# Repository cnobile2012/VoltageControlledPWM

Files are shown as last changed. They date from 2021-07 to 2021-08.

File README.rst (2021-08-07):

***************************************
Voltage-Controlled PWM Motor Controller
***************************************
The MIT License (MIT)

This circuit can supply either a 3.3 or 5 volt logic level PWM signal
depending on the reference voltage used. The voltage control input can also
be driven with either a 3.3 or 5 volt logic level signal depending on the
how the circuit is calibrated.

The PWM frequency can be adjusted in the range of 25K Hertz.

=======
LTspice
=======

Spice files for testing the circuit viability.

=====
KiCAD
=====

KiCAD files of the schematic and PCB.

========================
Calibration Instructions
========================

Test Equipment
--------------

  1. +12 and -12 Volt bench power supply.
  2. +5 or +3.3 Volt bench power supply.
  3. Variable voltage bench supply (0V-3.3V or 0V-5V).
  4. Multimeter
  5. Oscilloscope
  6. Frequency Counter (Optional--Can use the scope)

First, be sure your dual voltage power supply is as close to +12 and -12 volts
as possible. This will also be true in the actual environment that this PWM
will call home. If there is a slight offset between the absolute + and -
voltages there will also be a slight offset between the internal zero crossing
point of the triangle wave. Resistor R6 (460) can be adjusted to compensate for
this. The two trimmers R9 and R11 can also affect a slightly off zero crossing
by adjusting the complete on or off of the PWM, that is where a 0 control
voltage causes the output PWM to be 0 volts and the max 3.3/5 control voltage
causes the PWM to be 3.3/5 volts.

Calibration
-----------

  1. The R3 trimmer is used to adjust the internal triangle reference voltage.
     This should nominally be 10 volts peak-to-peak with the trimmer set to
     approximately 250K. Put your scope probes between TP2 (Triangle Wave) and
     TP0 (GND) then adjust R3.
  2. The R1 trimmer is used to adjust the frequency of the triangle wave. This
     should nominally be 25K Hertz with the trimmer set to approximately 24K.
     Put your scope or frequency counter probes between TP2 (Triangle Wave)
     and TP0 (GND) then adjust R1.
  3. The R9 trimmer is used to adjust the symmetry of the sweep voltage. This
     is the Control Voltage that adjusts the modulation of the PWM frequency.
     Adjust the variable power supply to 50% of 3.3V (1.65V) or 5V (2.5V)
     depending on your drive voltage then attach the supply to J3 and attach
     the multimeter probes to TP3 (Sweep) and TP0 (GND). Double check that the
     supply voltage is at 50% of your driving voltage then adjust R9 so the
     voltage on the multimeter is as close to 0 (zero) volts as possible.
  4. The R11 trimmer is used to set the peak-to-peak of the sweep voltage. Set
     the variable power supply to your drive voltage 5V or 3.3V and attach it
     to J3 (Voltage Control Input). Attach the multimeter probes to TP3 (Sweep)
     and TP0 (GND). Adjust R11 so that the multimeter shows plus 5V. Adjust the
     supply to 0 (zero) volts (or short the two pins on J3) and check that the
     voltage on the multimeter is -5V. See note 1 below.
  5. Check the PWM. Adjust the supply voltage to 50% as was done in step 3
     above and check that the PWM is 50%, then adjust the supply to 0 (zero)
     (or just short the two pins on J3) Check that the PWM is 0 (zero) volts.

Notes:

  1. In order to get 0 (full off) and 5/3.3 Volts (full on), on the PWM the
     sweep voltage may need to be slightly more than 10V peak-to-peak (R11)
     assuming the maximum triangle wave voltage is still 10V
     peak-to-peak. Adjusting the zero crossing with R9 may also be necessary.
  2. TP1 provides a square wave output, however it is not used in any of the
     calibrations.
  3. On Version 1.0 of the PCB the silk screen for the TPs (test points) are
     rather small and difficult to read. This will be fixed in version 2.0 of
     the PCB. The photos below should help with identifying which TP is which.

==============
PCBs Version 1
==============

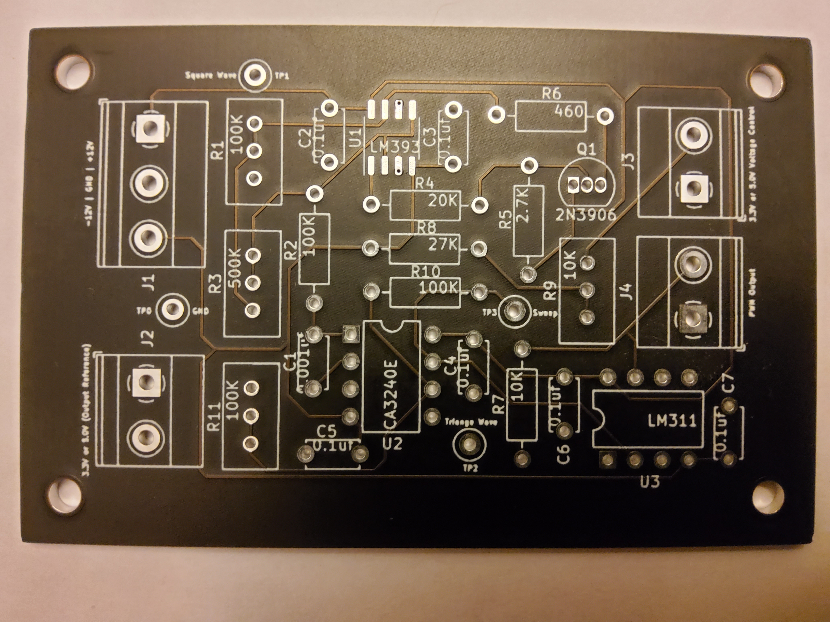
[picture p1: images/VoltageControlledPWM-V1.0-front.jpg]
Circuit board frontside image


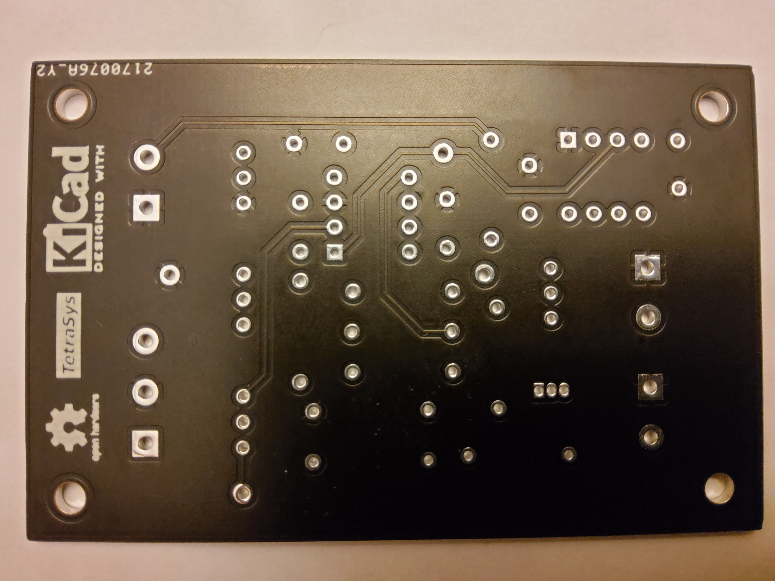
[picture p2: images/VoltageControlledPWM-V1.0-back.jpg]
Circuit board backside image


=========
Schematic
=========

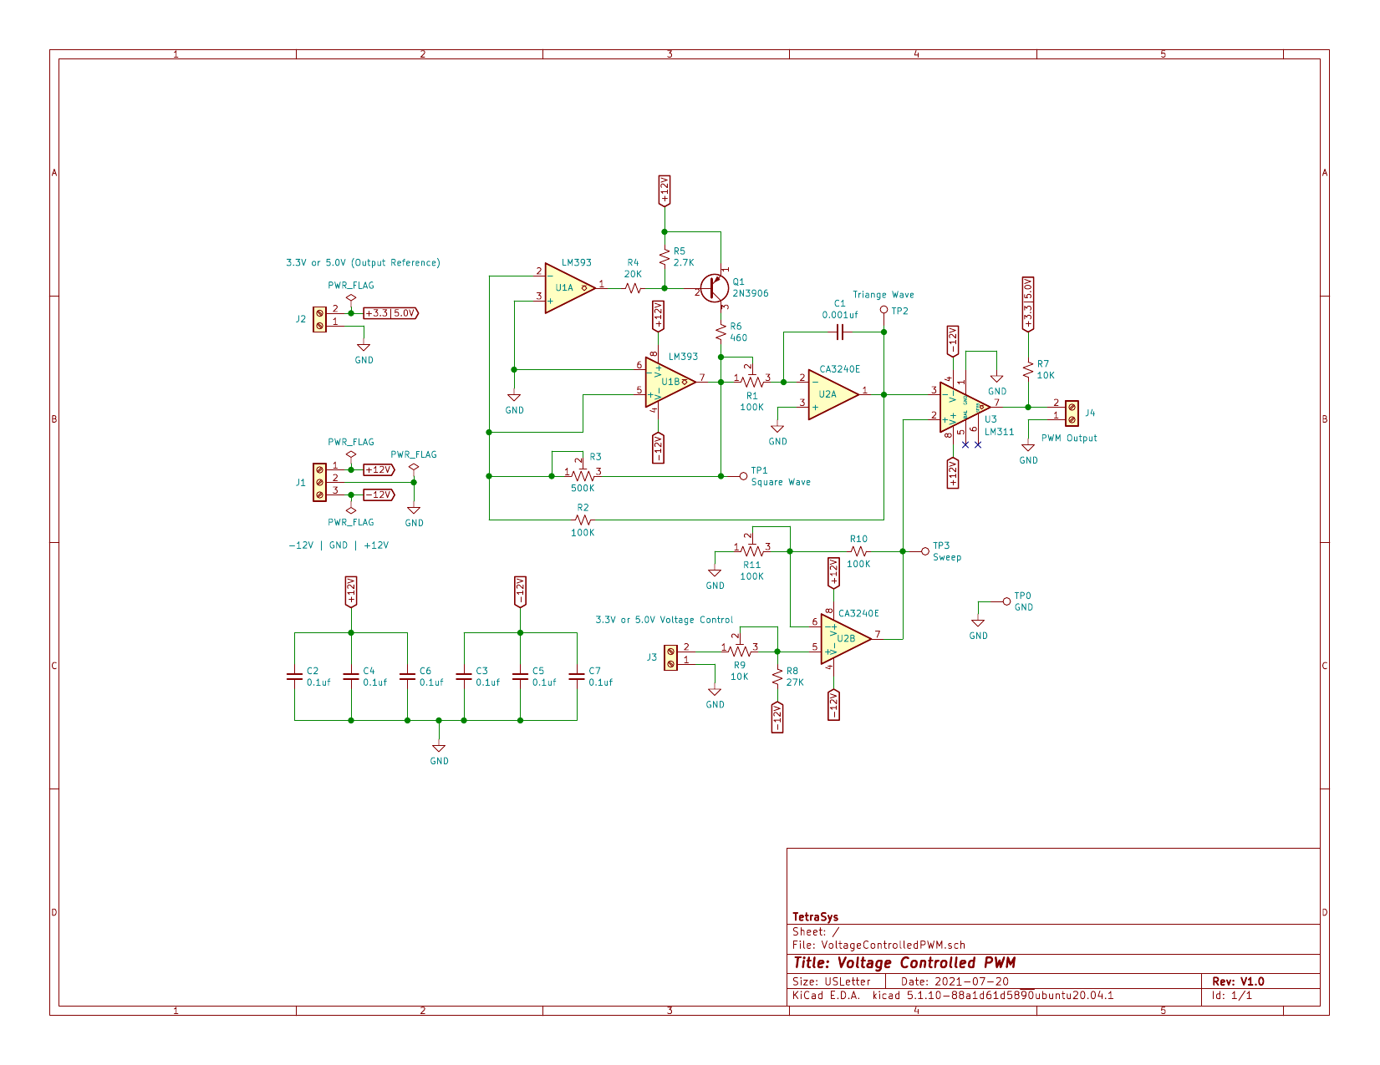
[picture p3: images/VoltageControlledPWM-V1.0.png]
Schematic


I want to give attribution to `Zero999 <https://www.eevblog.com/forum/beginners/simple-analog-function-generator-design/msg1174983/#msg1174983>`_
for the oscillator part of my circuit.

Feel free to contact me at: carl dot nobile at gmail.com

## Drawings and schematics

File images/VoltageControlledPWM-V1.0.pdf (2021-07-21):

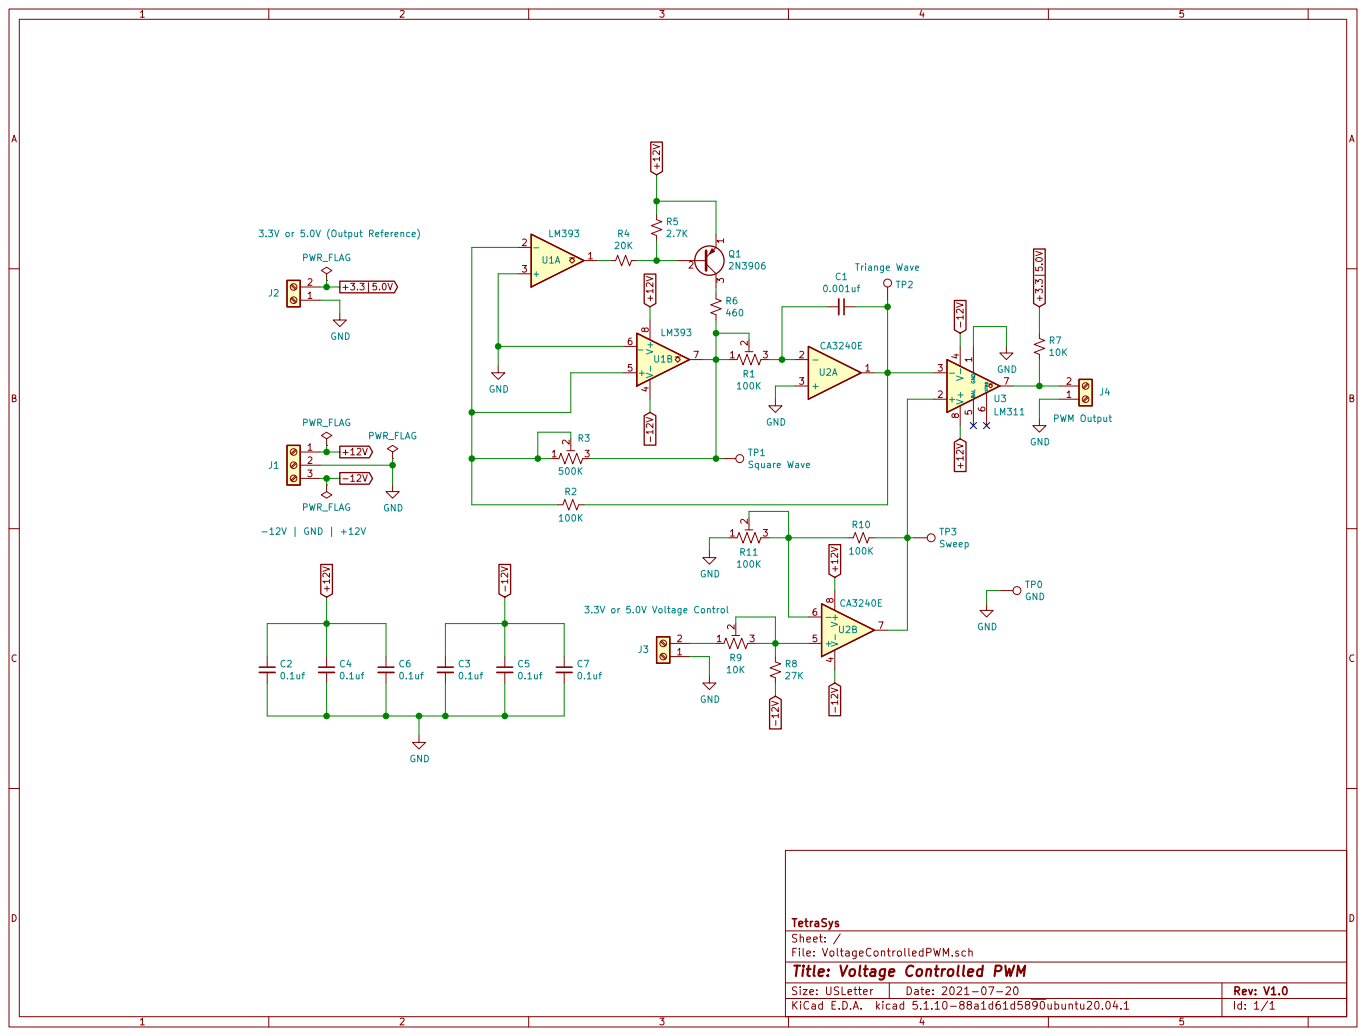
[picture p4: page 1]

TP3 Sweep TP2 Triange Wave TP1 Square Wave

File: VoltageControlledPWM.sch Sheet: / TetraSys

Id: 1/1 Title: Voltage Controlled PWM

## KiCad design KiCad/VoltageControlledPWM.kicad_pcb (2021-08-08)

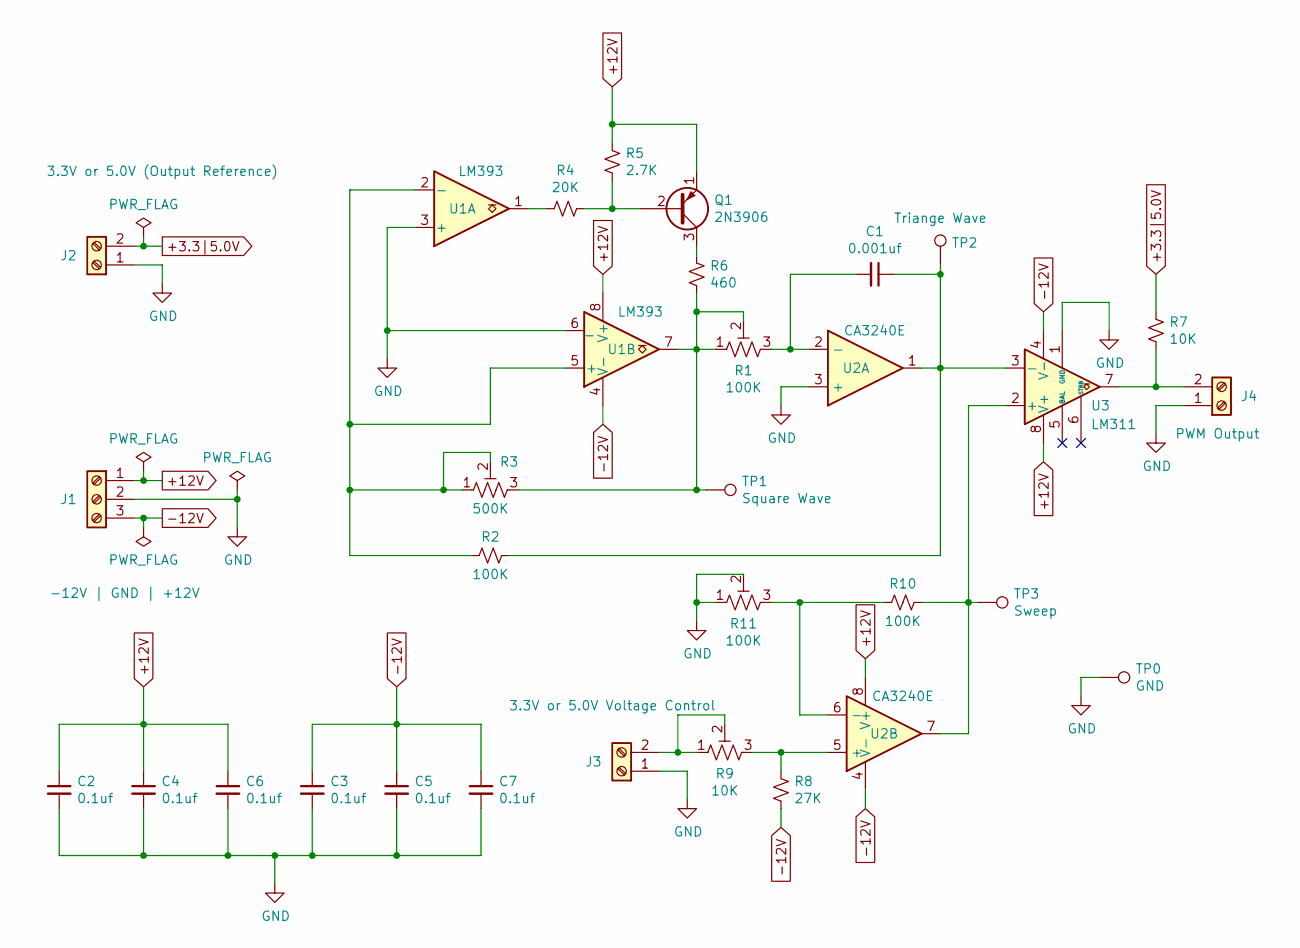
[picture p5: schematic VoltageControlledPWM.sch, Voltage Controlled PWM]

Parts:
C1: 0.001uf; C_Disc_D4.7mm_W2.5mm_P5.00mm
C2, C3, C4, C5, C6, C7: 0.1uf; C_Disc_D4.7mm_W2.5mm_P5.00mm
J1: -12V | GND | +12V; TerminalBlock_Phoenix_MKDS-1,5-3-5.08_1x03_P5.08mm_Horizont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
J2: 3.3V or 5.0V (Output Reference); TerminalBlock_Phoenix_MKDS-1,5-2-5.08_1x02_P5.08mm_Horizont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
J3: 3.3V or 5.0V Voltage Control; TerminalBlock_Phoenix_MKDS-1,5-2-5.08_1x02_P5.08mm_Horizont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
J4: PWM Output; TerminalBlock_Phoenix_MKDS-1,5-2-5.08_1x02_P5.08mm_Horizont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
Q1: 2N3906; TO-92_Inline
R1, R11: 100K; Potentiometer_Bourns_3296W_Vertical
R2, R10: 100K; R_Axial_DIN0207_L6.3mm_D2.5mm_P10.16mm_Horizontal
R3: 500K; Potentiometer_Bourns_3296W_Vertical
R4: 20K; R_Axial_DIN0207_L6.3mm_D2.5mm_P10.16mm_Horizontal
R5: 2.7K; R_Axial_DIN0207_L6.3mm_D2.5mm_P10.16mm_Horizontal
R6: 460; R_Axial_DIN0207_L6.3mm_D2.5mm_P10.16mm_Horizontal
R7: 10K; R_Axial_DIN0207_L6.3mm_D2.5mm_P10.16mm_Horizontal
R8: 27K; R_Axial_DIN0207_L6.3mm_D2.5mm_P10.16mm_Horizontal
R9: 10K; Potentiometer_Bourns_3296W_Vertical
TP0: GND; TestPoint_Loop_D2.50mm_Drill1.0mm
TP1: Square Wave; TestPoint_Loop_D2.50mm_Drill1.0mm
TP2: Triange Wave; TestPoint_Loop_D2.50mm_Drill1.0mm
TP3: Sweep; TestPoint_Loop_D2.50mm_Drill1.0mm
U1: LM393; SO-8_3.9x4.9mm_P1.27mm
U2: CA3240E; DIP-8_W7.62mm
U3: LM311; DIP-8_W7.62mm

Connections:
+3.3|5.0V: J2.2, R7.1
+12V: C2.1, C4.1, C6.1, J1.1, Q1.1 (E), R5.1, U1.8 (V+), U2.8 (V+), U3.8 (V+)
-12V: C3.1, C5.1, C7.1, J1.3, R8.2, U1.4 (V-), U2.4 (V-), U3.4 (V-)
GND: C2.2, C3.2, C4.2, C5.2, C6.2, C7.2, J1.2, J2.1, J3.1, J4.1, R11.1, R11.2, TP0.1, U1.3 (+), U1.6 (_), U2.3 (+), U3.1 (GND)
unnamed: C1.1, R2.1, TP2.1, U2.1, U3.3 (-)
unnamed: C1.2, R1.3, U2.2 (-)
unnamed: J3.2, R9.1, R9.2
unnamed: J4.2, R7.2, U3.7
unnamed: Q1.2 (B), R4.1, R5.2
unnamed: Q1.3 (C), R6.1
unnamed: R1.1, R1.2, R3.3, R6.2, TP1.1, U1.7
unnamed: R2.2, R3.1, R3.2, U1.2 (-), U1.5 (+)
unnamed: R4.2, U1.1
unnamed: R8.1, R9.3, U2.5 (+)
unnamed: R10.1, TP3.1, U2.7, U3.2 (+)
unnamed: R10.2, R11.3, U2.6 (-)

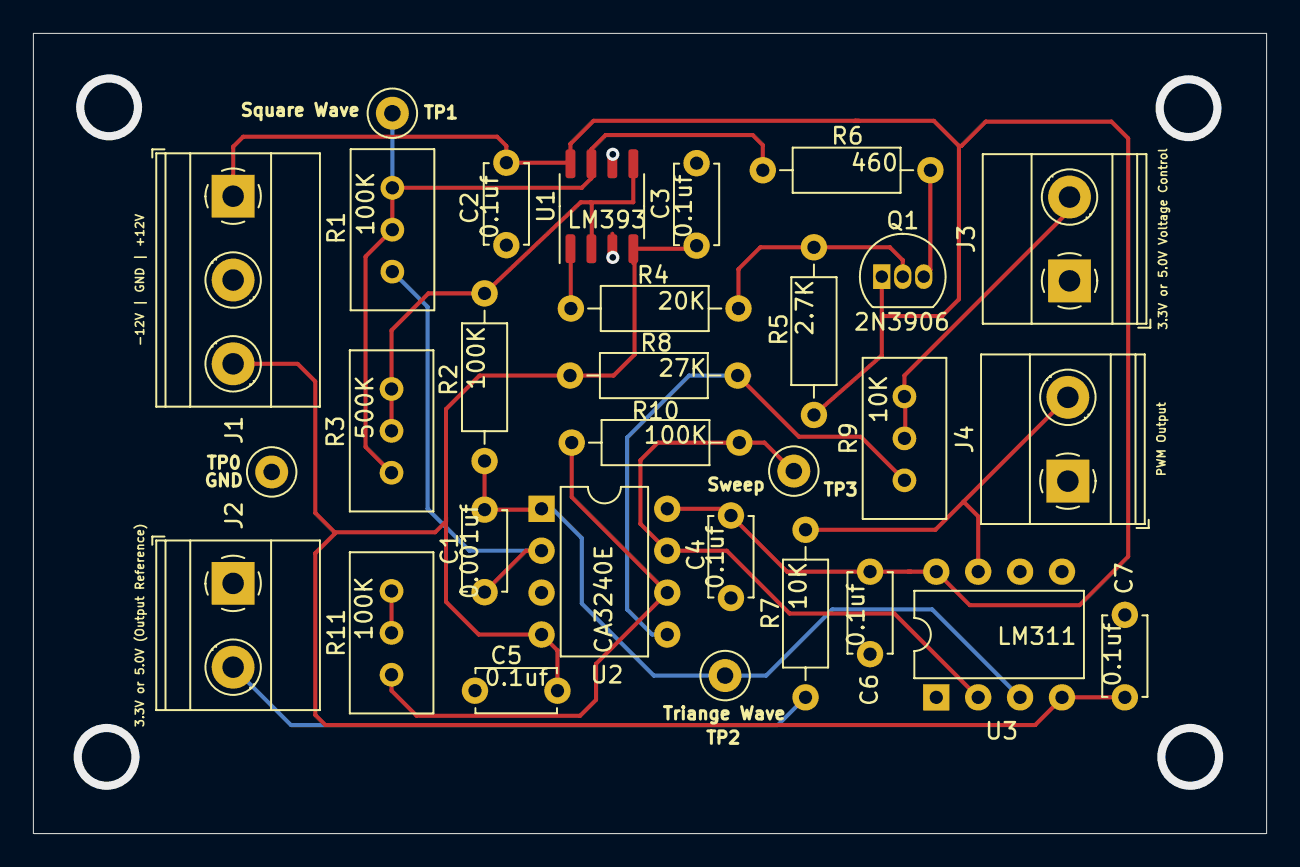
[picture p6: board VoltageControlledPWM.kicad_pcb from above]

Board: 2 copper layers, 74.8 x 48.5 mm, 30 parts (0 on the bottom side), 16 nets.

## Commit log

2021-07-18 Initial commit.
    [VoltageControlledPWM-B_Cu.gbr, VoltageControlledPWM-B_Mask.gbr, VoltageControlledPWM-B_Paste.gbr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]
2021-07-20 Latest updates
    [VoltageControlledPWM-B_Cu.gbr, VoltageControlledPWM-B_Mask.gbr, VoltageControlledPWM-B_Paste.gbr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]
2021-07-21 Updated to the board.
    [VoltageControlledPWM-B_Cu.gbr, VoltageControlledPWM-B_Mask.gbr, VoltageControlledPWM-B_Paste.gbr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]
2021-07-21 Added the schematic PDF file. and updated .gitignore.
2021-07-21 Added Logos.
    [VoltageControlledPWM-B_Cu.gbr, VoltageControlledPWM-B_Mask.gbr, VoltageControlledPWM-B_Paste.gbr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]
2021-08-07 Added images for the PCBs, updated both the README and the .gitignore files, and a minor update the LTSpice file.
2021-08-07 Updated the calibration instructions again.
2021-08-07 Updated the calibration instructions yet again.
2021-08-07 Added attribution for the ocilator part of my circuit.
2021-08-08 Fixes for version 2.0. Changed the direction of increase voltage on R9 and R11. Increased silkscreen size of TPs.
    [VoltageControlledPWM-B_Cu.gbr, VoltageControlledPWM-B_Mask.gbr, VoltageControlledPWM-B_Paste.gbr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]
